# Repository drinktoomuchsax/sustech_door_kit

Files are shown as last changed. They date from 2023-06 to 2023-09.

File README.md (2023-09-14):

<div>
<p align="center">
<a href="https://www.pixilart.com/art/sustech-door-kit-logo-sr20129901307f3" >
  sustech_door_kit_logo
</a>
  </p>  
<h1 align="center">
  南科大宿舍门锁套件
</h1>
<p align="center">
  丢掉你的校园卡
</p>
<p align="center">
人脸识别、模糊密码、电子反锁、访客密码、无痕恢复……</a>
</p>
</div>

_This page is not available in [English](README.en.md) yet._ 

                                                   

:unlock:这个项目使用两片ESP32开发板以及一系列模块，将宿舍开门体验提到了新高度

:star:欢迎Star

:+1:项目采用CC0协议，欢迎复刻、商用、传播

:poop:假如你想在此基础上开发新功能，看不懂屎山代码或有任何疑惑，欢迎issue

---

# :world_map:Table of Contents
- [功能](#功能)
- [原理](#原理)
- [复刻](#复刻)
  - [:money\_with\_wings:物料清单（全功能-预算敏感版本）](#money_with_wings物料清单全功能-预算敏感版本)
  - [:wrench:所需工具](#wrench所需工具)
  - [门的部分](#门的部分)
  - [门内模块（inModule）](#门内模块inmodule)
  - [门外模块（exModule）](#门外模块exmodule)
- [To Do](#to-do)

# 功能
![face recognition gif]()
![keyboard gif]()
![password define]()
![lock cant open gif]()
![random password generator]()
![single eye lock gif]()

# 原理
拆开门发现有调试的线，详见[博客](wait-to-be-writed)

# 复刻
本项目在开始之初的设计目标之一就是尽可能低的复刻门槛，所以使用的都是现成的市售模块。虽然牺牲了一些集成度和成本，但是你不需要经历繁复地采购和焊接贴片元件，只需少许简单焊接和组装就能复刻本项目。

如果对某一步的详细程度感到不满意或有任何疑惑，欢迎提交issue。

如果你的网络有问题不能加载出图片，可以看南科手册上的版本。

## :money_with_wings:物料清单（全功能-预算敏感版本）
> 第一步，下面全部买回来

| n | 名称 | 数量 | 款式 | 总价 | 链接 | 备注 |
| --- | --- | ---- | --- | --- | --- | --- |
| 0 | luat esp32-s3开发板 | 1片  | ESP32S3开发板 | ￥29.9 | [淘宝合宙旗舰店](https://item.taobao.com/item.htm?spm=a1z09.2.0.0.67002e8dnQlfYj&id=696836421009&_u=53t2jj8gb611) | 可以换其他家，但是记得修改pcb封装尺寸和代码引脚定义 |
| 1 | luat esp32-c3开发板 | 1片  | 经典款ESP32C3开发板 | ￥12.9 | [淘宝合宙旗舰店](https://item.taobao.com/item.htm?spm=a1z09.2.0.0.67002e8dnQlfYj&id=666579064570&_u=53t2jj8g0ed4) | 同上 |
| 2 | 人脸识别模块HLK-FR1002 | 1个  | 【强力推荐】测试套件B: FR1002单模块+端子连接线*1 | ￥72.5 | [淘宝海凌科旗舰店](https://detail.tmall.com/item.htm?id=693925937468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) | |
| 3 | 雷达模块HLK-LD2420 | 1个  | 【LD2420单模块】24G雷达模块（人体移动微动感应）  | ￥9.9 | [淘宝海凌科旗舰店](https://detail.tmall.com/item.htm?id=703242126067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) | |
| 4 | 内模块pcb打板 | 1片  | 略 | ￥20 | [Gerber文件](pcbDesign/imModule/inModule_Gerber.zip) | 嘉立创价格，可以换其他家，洞洞板手焊（￥2.5），立创eda抄板白嫖（￥0） |
| 5 | 外模块pcb打板 | 1片  | 略 | ￥40左右 | [Gerber文件](pcbDesign/exMoudle/sustech_door_kit-exModule-Gerber.zip) | 同上，但是需要两片，一片用作焊接，一篇用作背板安装 |
| 6 | 继电器 | 1个  | 4路5v红板 | ￥12 | [淘宝优信电子](https://item.taobao.com/item.htm?spm=a1z09.2.0.0.67002e8dnQlfYj&id=549692985984&_u=53t2jj8gef8e) | 要买5v的，不然不能开发板直接触发 |
| 6.1 | 16pin排母 | 6个  | 1*16P单排母座 | ￥1 | [淘宝优信电子](https://item.taobao.com/item.htm?spm=a230r.1.14.22.43cb7ce2fQNwRq&id=522579376259&ns=1&abbucket=13#detail) | 用来插开发板的。测试供电正常再插上去，不然会烧:(。并且如果每次更新固件都要整个拆下来，麻烦发 |
| 7 | :keyboard:轴体 | 14个 | cherryMX的封装就能够焊上，具体轴体按需选择 | ￥10 | [淘宝不知名店铺](https://item.taobao.com/item.htm?spm=a1z09.2.0.0.67002e8dnQlfYj&id=626986550029&_u=53t2jj8g20a3) | |
| 8 | :keyboard:键帽 | 12个 | 标准的十字孔能插上轴体就行 | ￥6.3 | [桃堡~或者去网吧悄悄扣走windows键~](https://item.taobao.com/item.htm?spm=a21n57.1.0.0.33f6523cuvqG1C&id=704738471960&ns=1&abbucket=0#detail) | 有实力可以加钱上点好的 |
| 9 | :nut_and_bolt:M3x25螺丝 | 5个  | 直径3mm，长度25mm，0.5螺距 | ￥0.3 | [1688](https://detail.1688.com/offer/572533111204.html?spm=a2615.2177701.autotrace-smt_offerGeneral.6.20a22b78zPF4M8) | 其实3个就够了，剩下2个惩罚不仔细看备注的强迫症 |
| 10 | :nut_and_bolt:M3x？？螺丝 | 4个  | 长度？？mm，其余同上 | ￥5.2 | [1688](https://detail.1688.com/offer/572533111204.html?spm=a2615.2177701.autotrace-smt_offerGeneral.6.20a22b78zPF4M8) | 算上邮费 |
| 11 | :nut_and_bolt:M3螺母 | 4个  | 直径M3，六角对边长5.5mm，螺距0.5mm，2.4mm厚 | ￥0.2 | [1688](https://detail.1688.com/offer/572533111204.html?spm=a2615.2177701.autotrace-smt_offerGeneral.6.20a22b78zPF4M8) | 邮费算在上面了 |
| 12 | :nut_and_bolt:M3防松螺母  | 3个  | 长度？？mm，其余同上 | ￥0.2 | [1688](https://detail.1688.com/offer/572533111204.html?spm=a2615.2177701.autotrace-smt_offerGeneral.6.20a22b78zPF4M8) | 用来分隔继电器和内模块，邮费算在上面了 |
| 13 | :electric_plug:硅胶线 | 4条  | 统一1m，18AWG；红色、黑色、黄色、白色 | ￥6 | [桃堡](https://item.taobao.com/item.htm?spm=a1z09.2.0.0.67002e8dnQlfYj&id=654286714565&_u=53t2jj8g48c8) | |
| 14 | :electric_plug:CtoC数据线 | 1条  | 1m左右就好 | ￥6 | [桃堡](https://detail.tmall.com/item.htm?id=662435210626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) | 如果你经常有连接开发板的需求，推荐合宙的[10条各种版本打包](https://item.taobao.com/item.htm?spm=a1z10.5-c-s.w4002-24045920841.24.230e5aa3n5OKyx&id=706207670841) |
| 15 | DC-DC模块 | 1个  | 链接里就一个，买他就好 | ￥5.7 | [桃堡](https://item.taobao.com/item.htm?spm=a1z09.2.0.0.35b32e8dcWQ58H&id=536347025767&_u=53t2jj8g6082) | |
| **666** | **总计** | | | **￥240左右** |

### :moneybag:物料清单（删减功能-预算敏感版本）
如果上述BOM超过了你的预算，可以通过删减功能来减少部件，比如可以删减掉人脸识别功能，避免购买HLK-FR1002和HLK-LD2420将价格减到**153元**。

或者可以eda抄板，节省打板价格。**注意，外模块尺寸为5*13cm，不在立创优惠劵的尺寸范围内，可以试着删减掉人脸识别后将尺寸缩小。**

砍掉一些功能，花上几个小时抄板，修改一下代码，理论最低预算为**86元**。

## :wrench:所需工具
> 如果只是为了复刻项目，下面这些工具不用全部买回来，想办法借到比较合理。但这是个社恐友好的项目，所以放上一些参考购买链接。

| 名称 | 用途 | 参考购买链接 |
| --- | --- | --- |
| 剥线钳 | 剥线 | [【简装】7寸单色手柄剥线钳](https://detail.tmall.com/item.htm?abbucket=0&id=43540267171&ns=1&spm=a21n57.1.0.0.1f6d523cvhBHgo) |
| 烙铁 | 焊接 | [标配+C2C数据线+转接板+氮化镓充电器+K65小刀头+BC2尖头 ](https://detail.tmall.com/item.htm?id=662514528915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) |
| 焊锡 | 焊接 | [含锡40%线径0.8mm-50克](https://detail.tmall.com/item.htm?id=595763429832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) |
| 十字螺丝刀 | 打螺丝 | [5*75十字【专业款】](https://item.taobao.com/item.htm?spm=a21n57.1.0.0.33f6523cuvqG1C&id=709830788462&ns=1&abbucket=0#detail) |
| 扳手 | 打螺母 | [【中小型】活扳手/管钳双功能两用8寸-200mm](https://detail.tmall.com/item.htm?id=655191633412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) |
| 胶布 | 防止短接 | 是个胶布就行 |
| 美工刀或笔刀 | 剥线 | 最好锋利一点 |
| 热熔胶枪 | 加固剥线处 | [50W豪华小胶枪+ 10胶棒](https://detail.tmall.com/item.htm?id=559404680156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) |

## 门的部分
### 1.拆门

> 首先，这部分不适合一个人，建议你找一个室友帮忙

> **门只能从内部拆开，平时能够看到2颗裸露的螺丝，大胆地拆。**

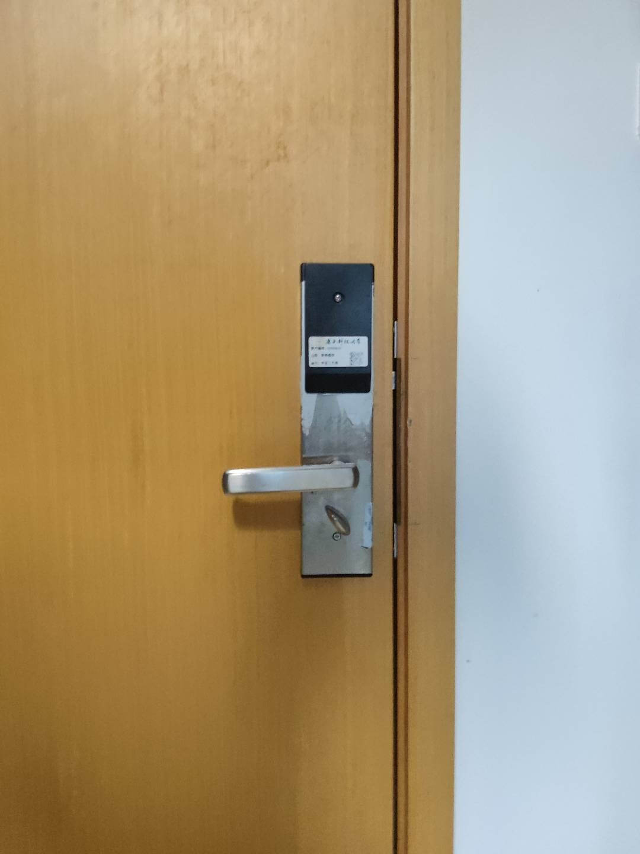
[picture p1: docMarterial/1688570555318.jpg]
一上一下正好两个


> **拆开后把塑料外壳取下，能看到三颗螺丝,前面两颗，后面一颗。拆掉前面两颗整个把手就会掉下来。**

> 这时你应该可以看到内门把手小锁的销被取走了，这就是我们不能从里面反锁的原因。网上没找到合适的，你有时间可以自己建模3D打印一个就能重新获得机械反锁门的能力。

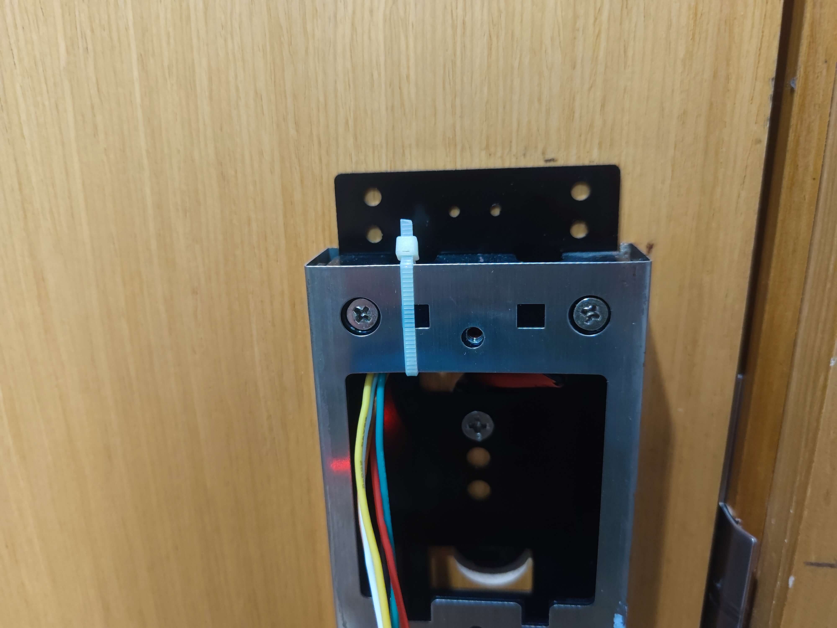
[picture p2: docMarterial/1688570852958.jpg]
前面两颗，后面一颗


> 因为这部分是后写的，有一些照片因为安装了内模块不能继续拍，sorry

> **内门把手掉下来后，会露出一个框架，有两颗螺丝，这两颗螺丝固定内框架和外门把手**

> 下图是一个，还有一个在更下方

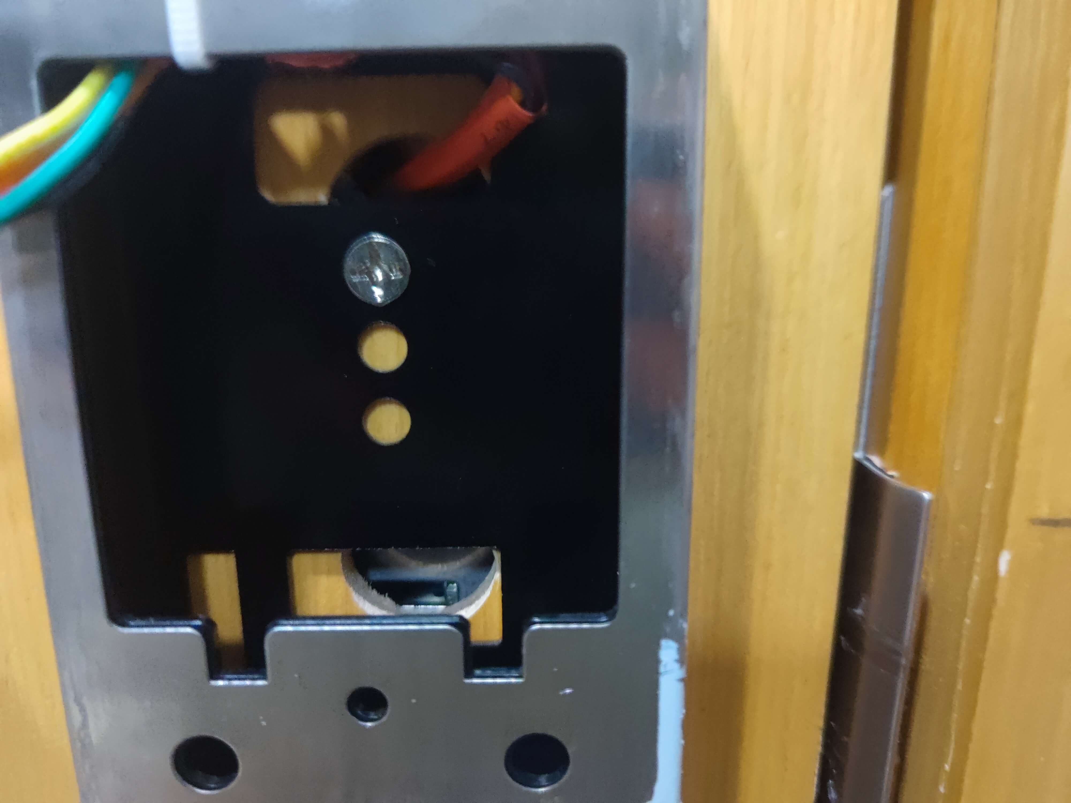
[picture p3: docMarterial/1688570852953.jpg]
上方的螺丝


> **一手扶着外门把手，一手拆内框架的螺丝**

> **螺丝拆下来后，内框架会掉下来，外门把手也会掉下来**

> **你应该可以看到掉下来的外门把手框里有一些线连到门里面（忽略图片左方的凝固的热熔胶）**

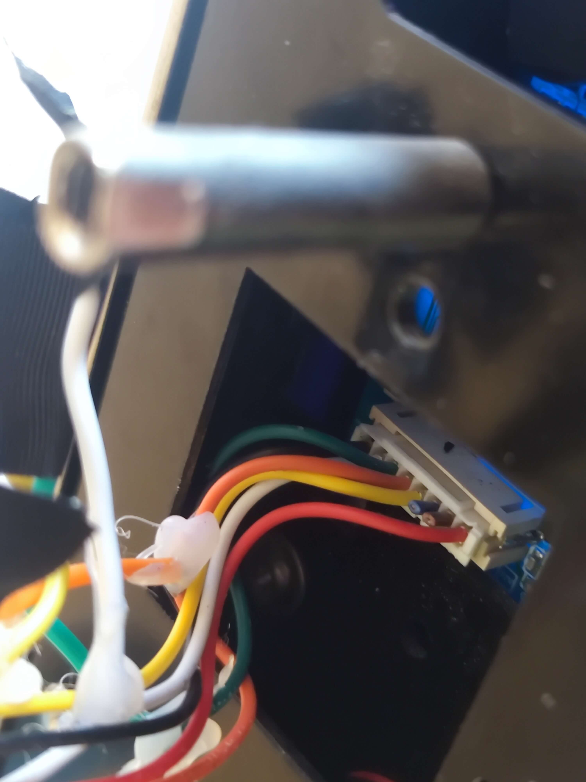
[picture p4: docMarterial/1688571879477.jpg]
线们


> **这些线有不同的功能，红线12v供电、黑线地，其他四个颜色短接地会有不同的效果，效果如下表**

| 短接 | 效果 |
| ---- | --- |
| 黑橙 | 面板变绿，正常开门 |
| 黑绿 | 锁门（面板保持蓝色） |
| 黑黄 | 开门 |
| 黑白 | 锁门（面板变红） |

> **你已经看到线了，进入下一步，剥线！**

### 2.剥线

> **这是一个手艺活，比较考验耐心**

> **你需要用美工刀或者笔刀将线的外层剥开，露出里面的金属。注意不要直接切断，特别是红色和黑色的电源线，没人知道这个系统断电重启之后还可能会出现哪些问题**

> **项目只会用到4根线，分别是红色、黑色、黄色、白色。所以你只需要剥4根线**

### 3.焊接延长线

> 这一步可能会比较难

> **线剥好后，剪下你买的[硅胶线](https://item.taobao.com/item.htm?spm=a1z09.2.0.0.67002e8dnQlfYj&id=654286714565&_u=53t2jj8g48c8)，长度需要自己估计一下，大概40cm（估计值，绝对不准）。用[剪线钳](https://detail.tmall.com/item.htm?abbucket=0&id=43540267171&ns=1&spm=a21n57.1.0.0.1f6d523cvhBHgo)剥去两头的线。一端镀锡，一端缠胶布备用**

> **然后给外门把手剥线的地方也镀上锡**

> **然后把对应颜色的线焊上**

> **打上热熔胶防止短接同时加强连接处**

> **最后效果如下（方便研究我把所有都剥了）**

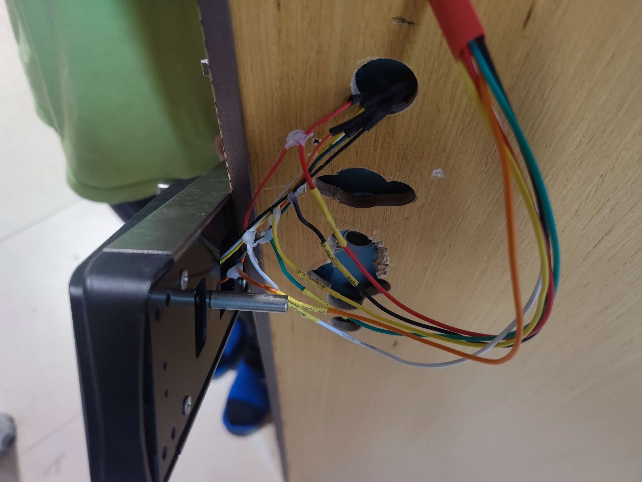
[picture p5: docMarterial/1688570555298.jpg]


### 4.走线
> **把线首先穿过外门把手上面的小框**

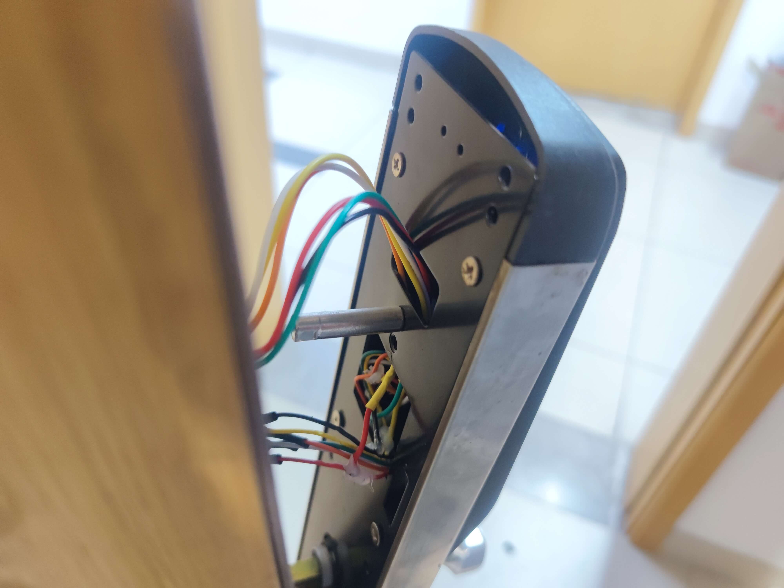
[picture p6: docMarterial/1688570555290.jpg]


> **然后穿过门上的洞，这样外门把手就不会因为线的存在而不能贴合门体**

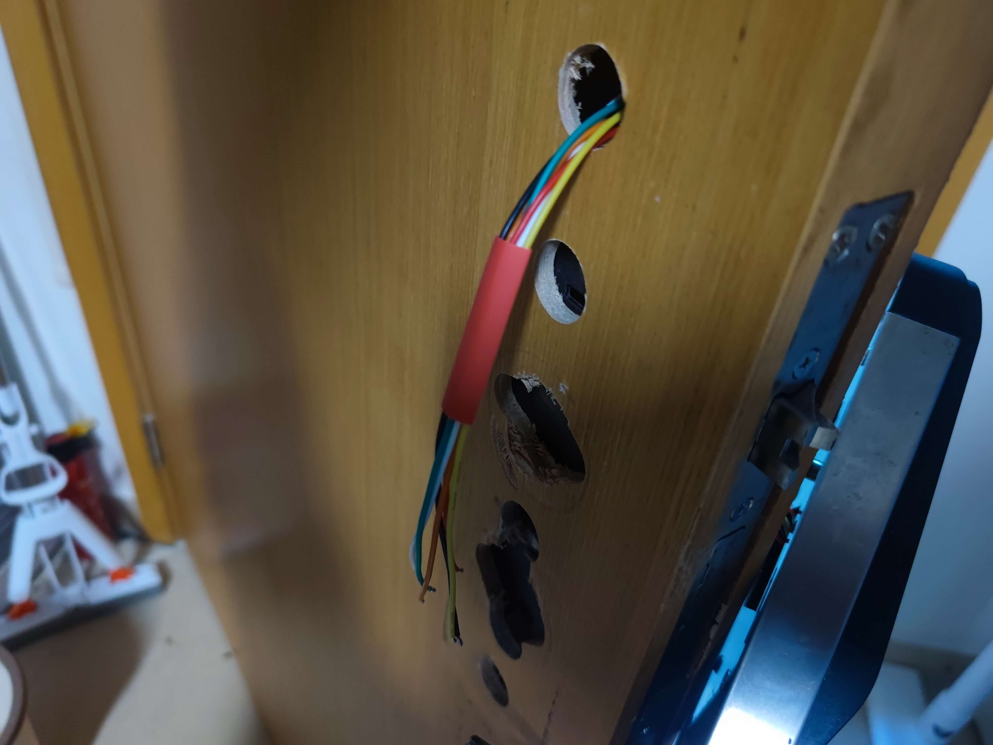
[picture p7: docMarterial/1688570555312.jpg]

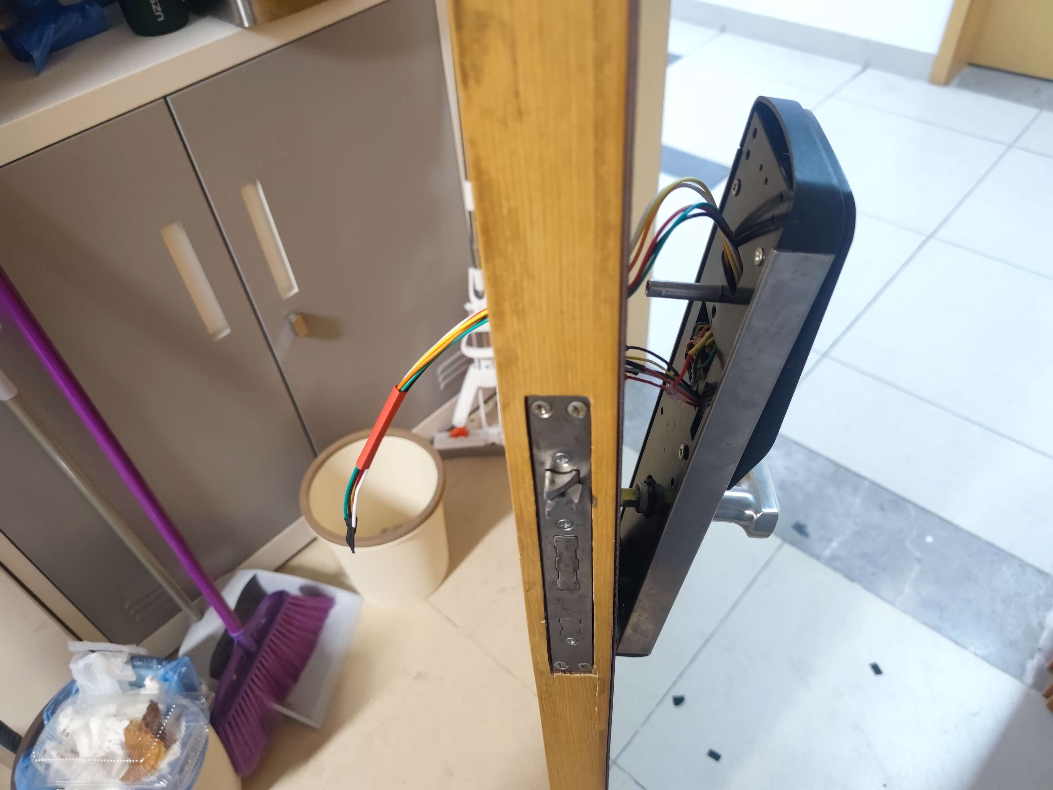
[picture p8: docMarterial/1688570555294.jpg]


> **最后效果如下，平整度没有差别**

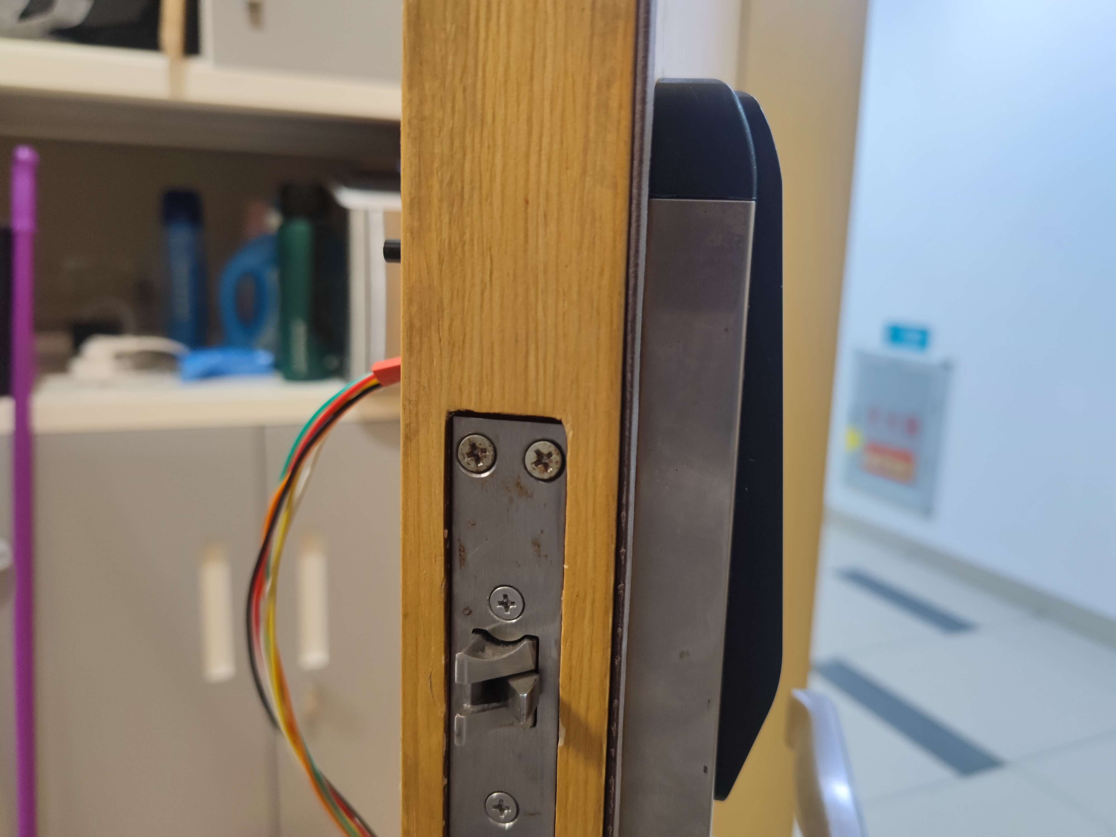
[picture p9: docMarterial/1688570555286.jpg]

### 5.装门

> **然后就是逆向装回去的过程，不多说了**

> **唯一值得注意的点是，可以用一段胶布缠上整束线，然后用一个扎带固定，这样就把拉力转移到扎带部分而不是焊点** 

zipper

> **最后效果如下**

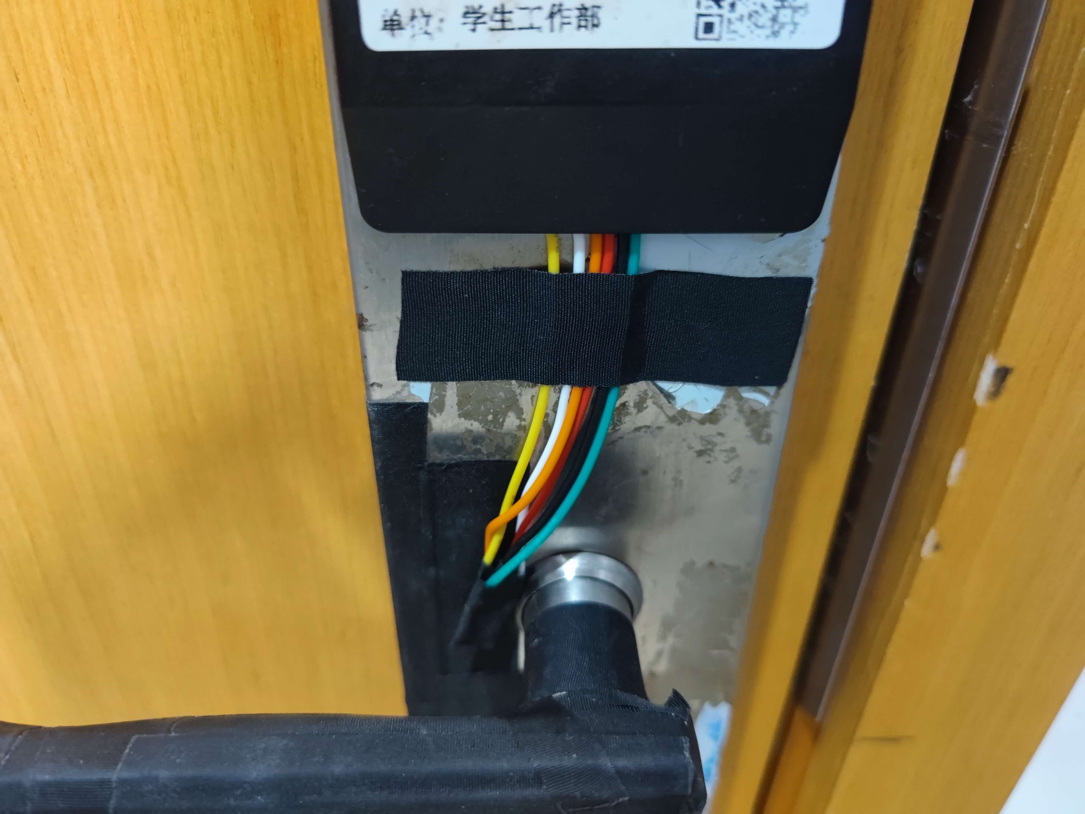
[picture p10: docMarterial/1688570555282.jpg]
cables on the door


> 至此拆门部分结束

## 门内模块（inModule）

### 1.焊接
#### a.开发板排母
#### b.排线
### 2.开发板刷入程序
#### a.更改参数
- bleServerName
- BLE UUIDs
- WiFi name
- WiFi pswd
- realpswd
- 
### 3.安装
#### a.继电器接门内地线
#### b.继电器接开发版控制线、电源线、地线
#### c.测试输出电压
#### d.安装开发板
#### e.热熔胶胶固定
#### f.焊接门内12v电源线

### 4.测试
#### a.WiFi开门功能
#### b.按键功能

## 门外模块（exModule）
### 1.焊接
#### a.电阻、开发板
#### b.雷达、排针
#### c.人脸识别模块

### 2.组装
### 3.开发板刷入程序
#### a.更改参数
### 4.配置模块
#### a.人脸注册
#### b.修改雷达门限
### 5.调试

# To Do
对功能有任何想法和提议，都欢迎提交issue。当然，保证不保证解决。
- [ ] 完善文档
- [ ] 接入homeassistant，让小爱同学开门
- [ ] 通信协议
- [ ] 剩下的两根线
- [ ] 更多的功能
- [ ] 更低的复刻门槛

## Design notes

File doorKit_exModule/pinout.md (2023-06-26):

|IO选择|对应功能|IO编号|启动项相关|ADC|DAC|UART|Touch|SPI/IIC|
|:----|:----|:----|:----|:----|:----|:----|:----|:----|
| | |GPIO0|下载：低电平/启动：高电平|ADC2_1| | |TP_1| |
| | |GPIO1| | | |TX0| | |
| | |GPIO2| |ADC2_2| | |TP_2| |
| | |GPIO3| | | |RX0| | |
|x|keyboardInput|GPIO4| |ADC2_0| | |TP_0| |
| | |GPIO5|启动时必须高电平| | | | |VSPI|
| | |GPIO6|连接了FLASH(CLK)| | | | | |
| | |GPIO7|连接了FLASH(SD0)| | | | | |
| | |GPIO8|连接了FLASH(SD1)| | | | | |
| | |GPIO9|连接了FLASH(SD2)| | |RX1| | |
| | |GPIO10|连接了FLASH(SD3)| | |TX1| | |
| | |GPIO11|连接了FLASH(CMD)| | | | | |
| | |GPIO12|启动时必须低电平|ADC2_5| | |TP_5|HSPI|
| | |GPIO13| |ADC2_4| | |TP_4|HSPI|
| | |GPIO14|启动时必须高电平|ADC2_6| | |TP_6|HSPI|
| | |GPIO15|启动时必须高电平|ADC2_3| | |TP_3|HSPI|
| | |GPIO16| | | |RX2| | |
| | |GPIO17| | | |TX2| | |
| | |GPIO18| | | | | |VSPI|
| | |GPIO19| | | | | |VSPI|
|x|keyboardOutput|GPIO21| | | | | |IIC_SDA|
|x|keyboardOutput|GPIO22| | | | | |IIC_SCL|
|x|keyboardOutput|GPIO23| | | | | |VSPI|
| | |GPIO25| |ADC2_8|DAC_1| | | |
| | |GPIO26| |ADC2_9|DAC_2| | | |
| | |GPIO27| |ADC2_7| | |TP_7| |
|x|keyboardInput|GPIO32| |ADC1_4| | |TP_9| |
|x|keyboardInput|GPIO33| |ADC1_5| | |TP_8| |
| ||GPIO34|Input Only|ADC1_6| | | | |
|x|keyboardInput|GPIO35|Input Only|ADC1_7| | | | |
| | |GPIO36|Input Only/SVP|ADC1_0| | | | |
| | |GPIO39|Input Only/SVN|ADC1_3| | | | |
| | |GND||| | | | |
| | |GND||| | | | |
| | |3V3||| | | | |
| | |VIN||| | | | |

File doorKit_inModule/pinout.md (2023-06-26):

|IO选择|对应功能|IO编号|启动项相关|ADC|DAC|UART|Touch|SPI/IIC|
|:----|:----|:----|:----|:----|:----|:----|:----|:----|
| | |GPIO0|下载：低电平/启动：高电平|ADC2_1| | |TP_1| |
| | |GPIO1| | | |TX0| | |
| | |GPIO2| |ADC2_2| | |TP_2| |
| | |GPIO3| | | |RX0| | |
|x|Touch pad|GPIO4| |ADC2_0| | |TP_0| |
| | |GPIO5|启动时必须高电平| | | | |VSPI|
| | |GPIO6|连接了FLASH(CLK)| | | | | |
| | |GPIO7|连接了FLASH(SD0)| | | | | |
| | |GPIO8|连接了FLASH(SD1)| | | | | |
| | |GPIO9|连接了FLASH(SD2)| | |RX1| | |
| | |GPIO10|连接了FLASH(SD3)| | |TX1| | |
| | |GPIO11|连接了FLASH(CMD)| | | | | |
| | |GPIO12|启动时必须低电平|ADC2_5| | |TP_5|HSPI|
| | |GPIO13| |ADC2_4| | |TP_4|HSPI|
| | |GPIO14|启动时必须高电平|ADC2_6| | |TP_6|HSPI|
| | |GPIO15|启动时必须高电平|ADC2_3| | |TP_3|HSPI|
| | |GPIO16| | | |RX2| | |
| | |GPIO17| | | |TX2| | |
| | |GPIO18| | | | | |VSPI|
|x|relay ouput|GPIO19| | | | | |VSPI|
|x|relay ouput|GPIO21| | | | | |IIC_SDA|
|x|relay ouput|GPIO22| | | | | |IIC_SCL|
|x|relay ouput|GPIO23| | | | | |VSPI|
| | |GPIO25| |ADC2_8|DAC_1| | | |
| | |GPIO26| |ADC2_9|DAC_2| | | |
| | |GPIO27| |ADC2_7| | |TP_7| |
| | |GPIO32| |ADC1_4| | |TP_9| |
| | |GPIO33| |ADC1_5| | |TP_8| |
| | |GPIO34|Input Only|ADC1_6| | | | |
| | |GPIO35|Input Only|ADC1_7| | | | |
| | |GPIO36|Input Only/SVP|ADC1_0| | | | |
| | |GPIO39|Input Only/SVN|ADC1_3| | | | |
|x|GND for relay|GND||| | | | |
|x|Powe in|GND||| | | | |
| | |3V3||| | | | |
|x|Power in|VIN||| | | | |

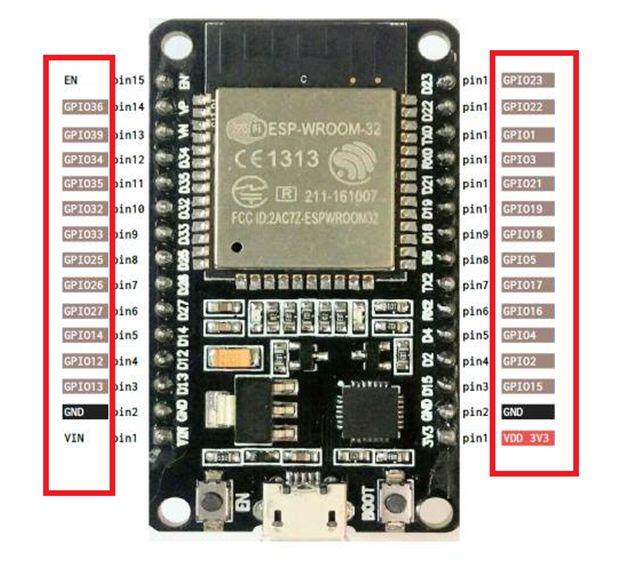
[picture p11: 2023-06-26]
tool/devKit/32S.jpg

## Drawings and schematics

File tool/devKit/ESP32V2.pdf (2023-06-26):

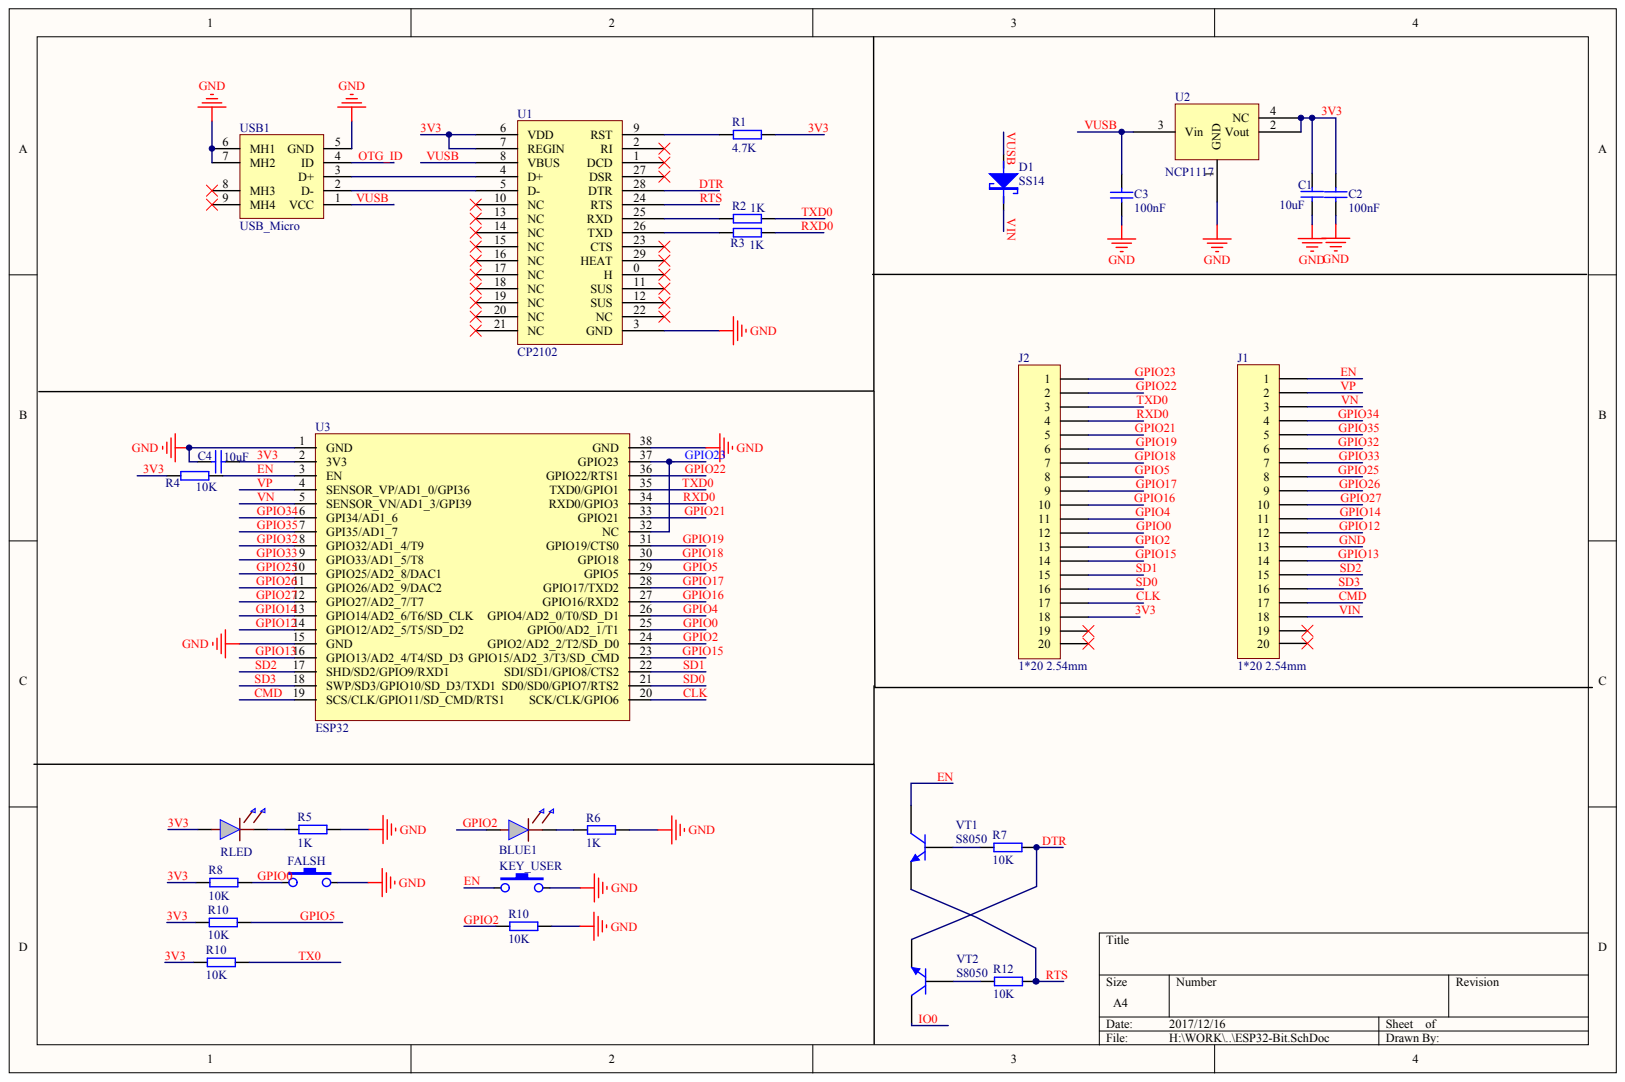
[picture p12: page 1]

GND 1 Vout 2 Vin 3 NC 4

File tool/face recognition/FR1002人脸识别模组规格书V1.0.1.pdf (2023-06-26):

# HLK-

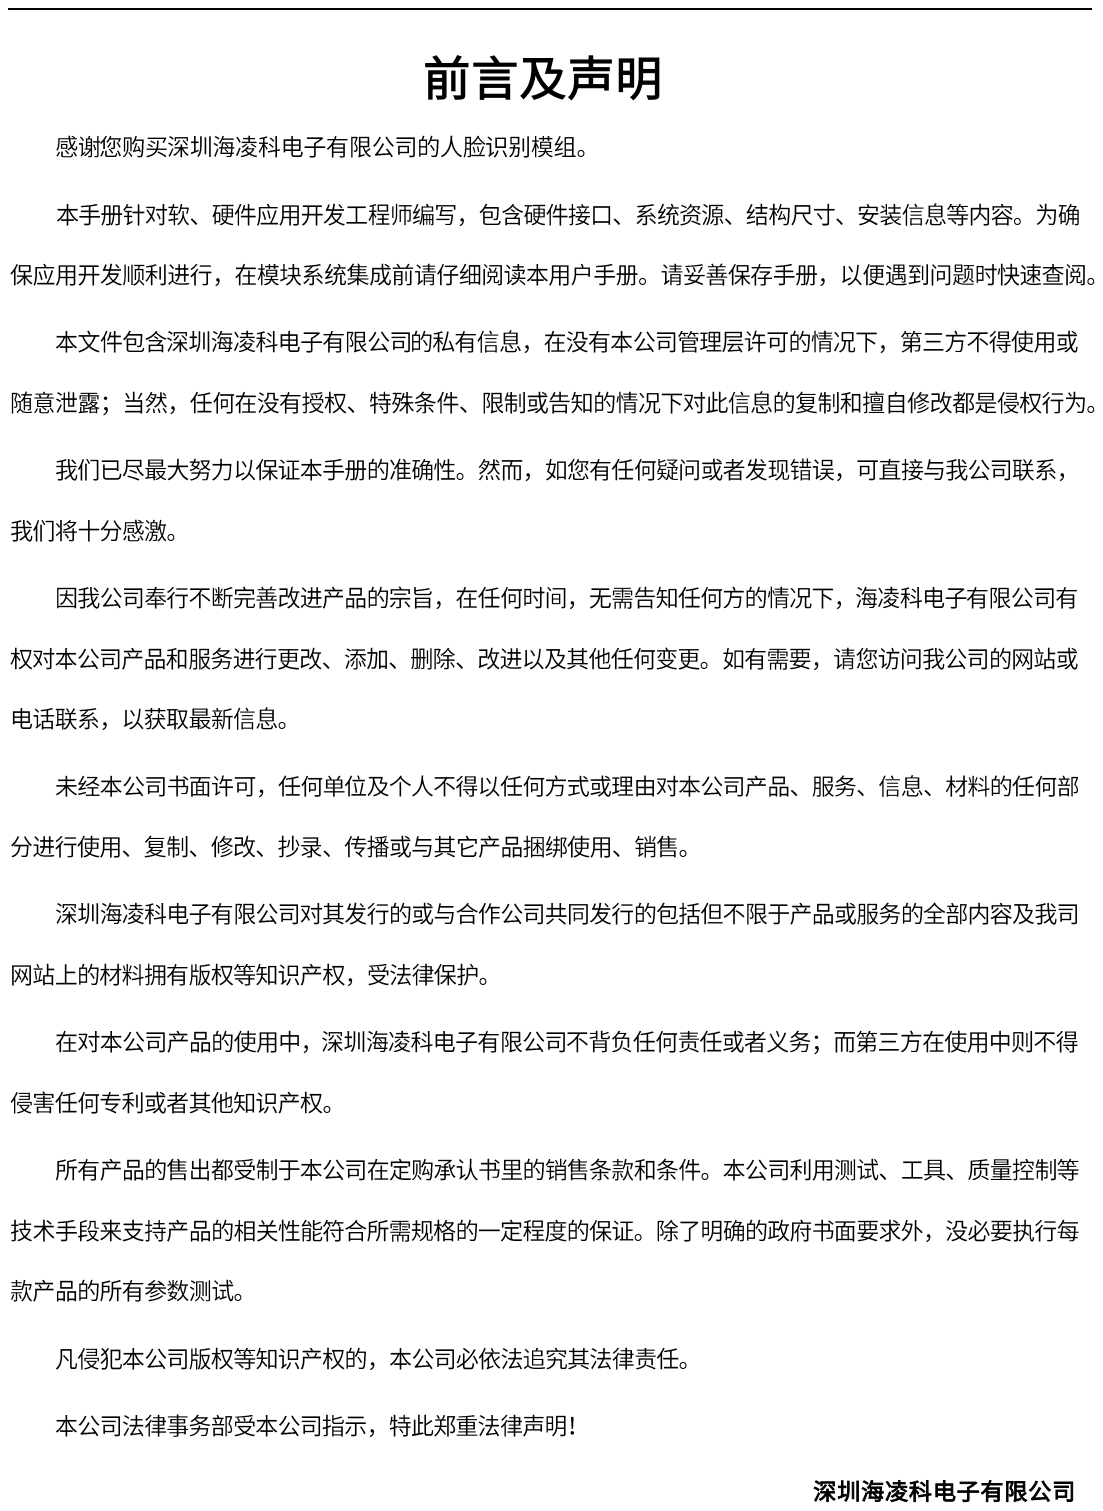
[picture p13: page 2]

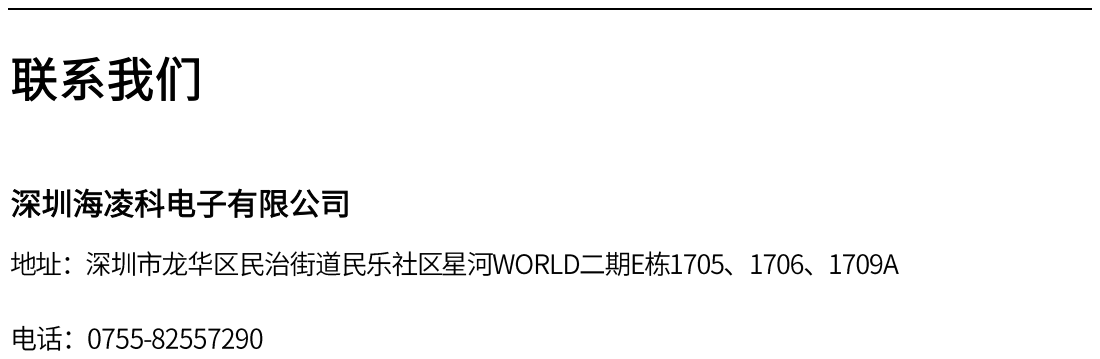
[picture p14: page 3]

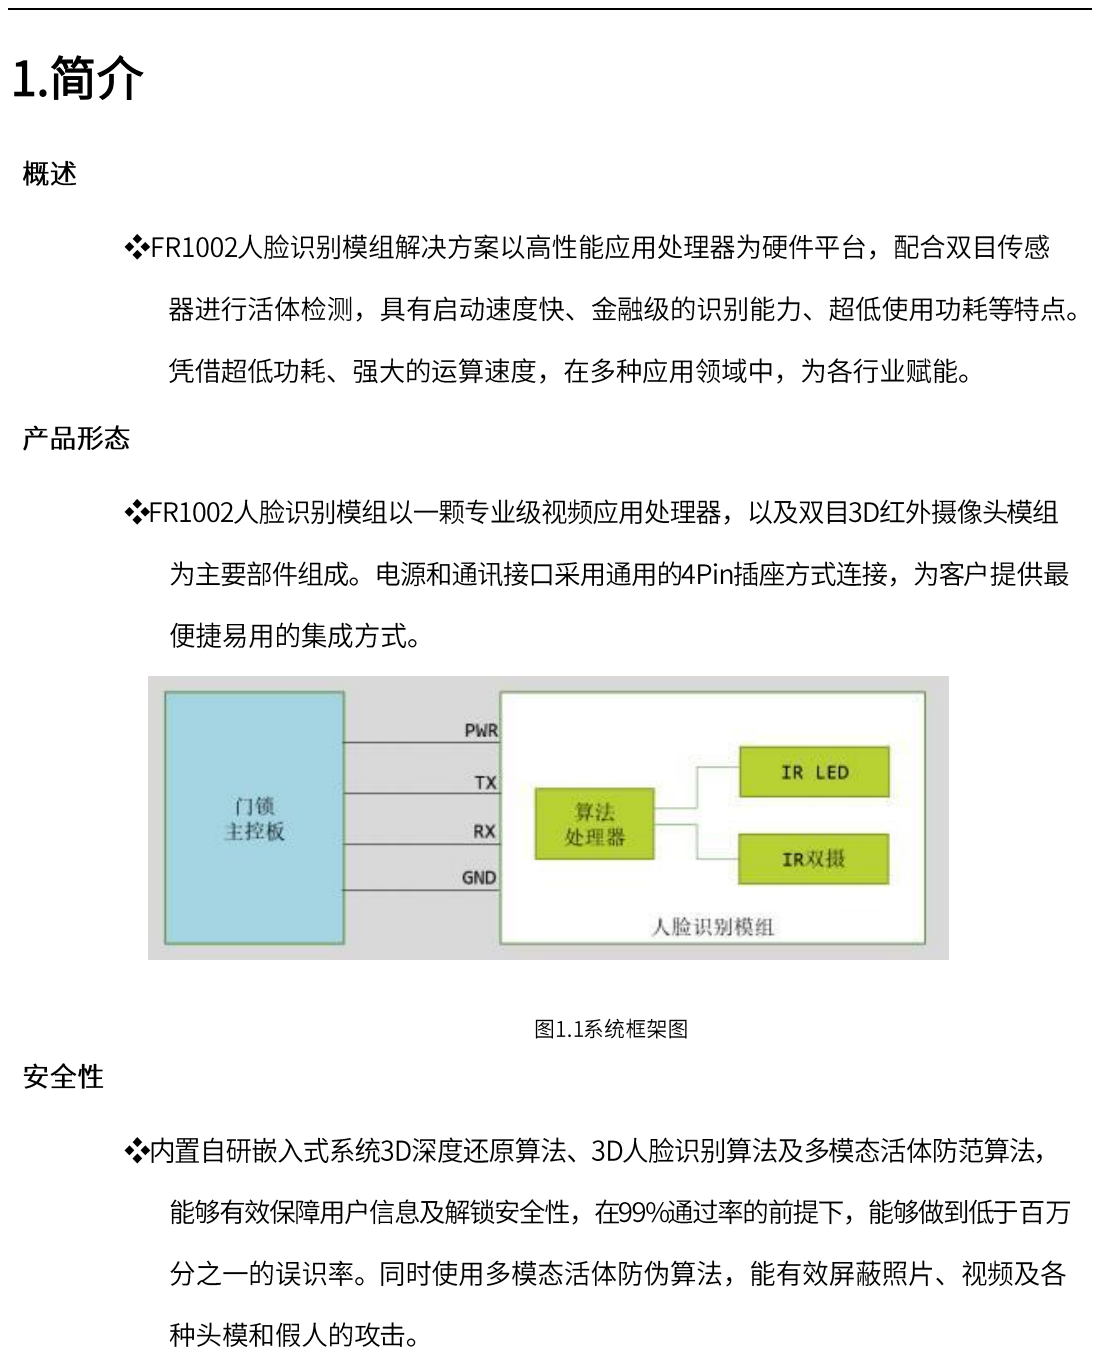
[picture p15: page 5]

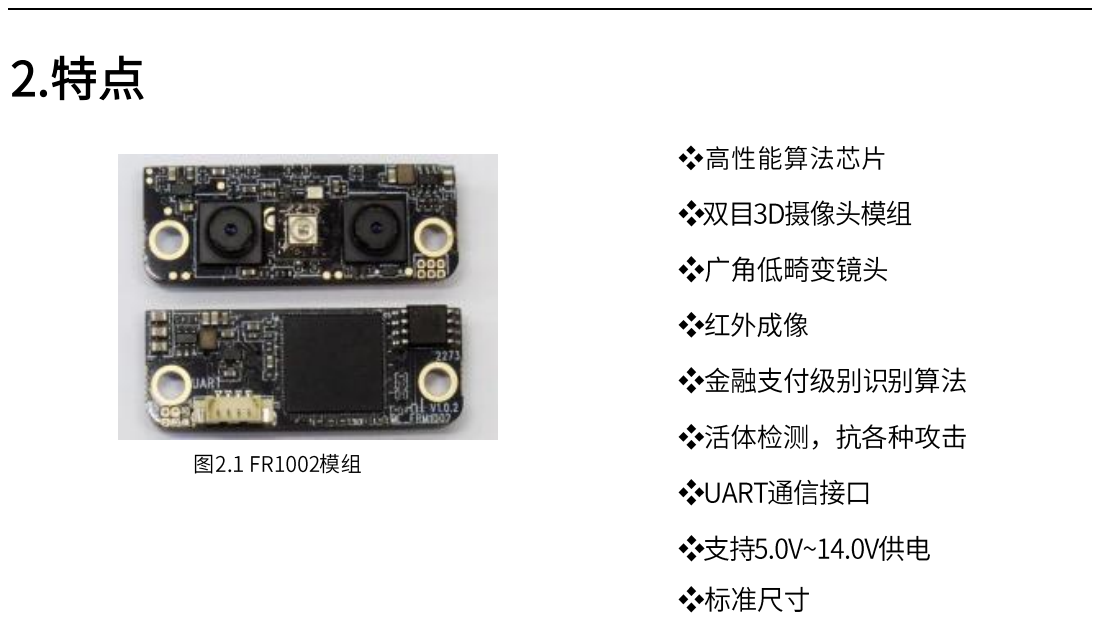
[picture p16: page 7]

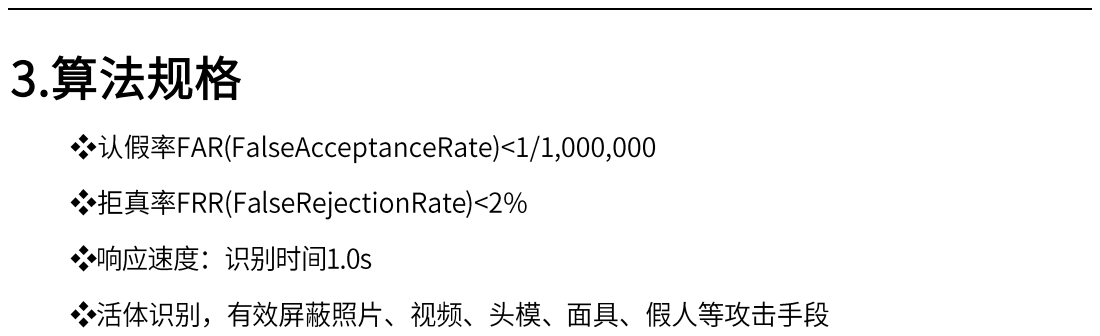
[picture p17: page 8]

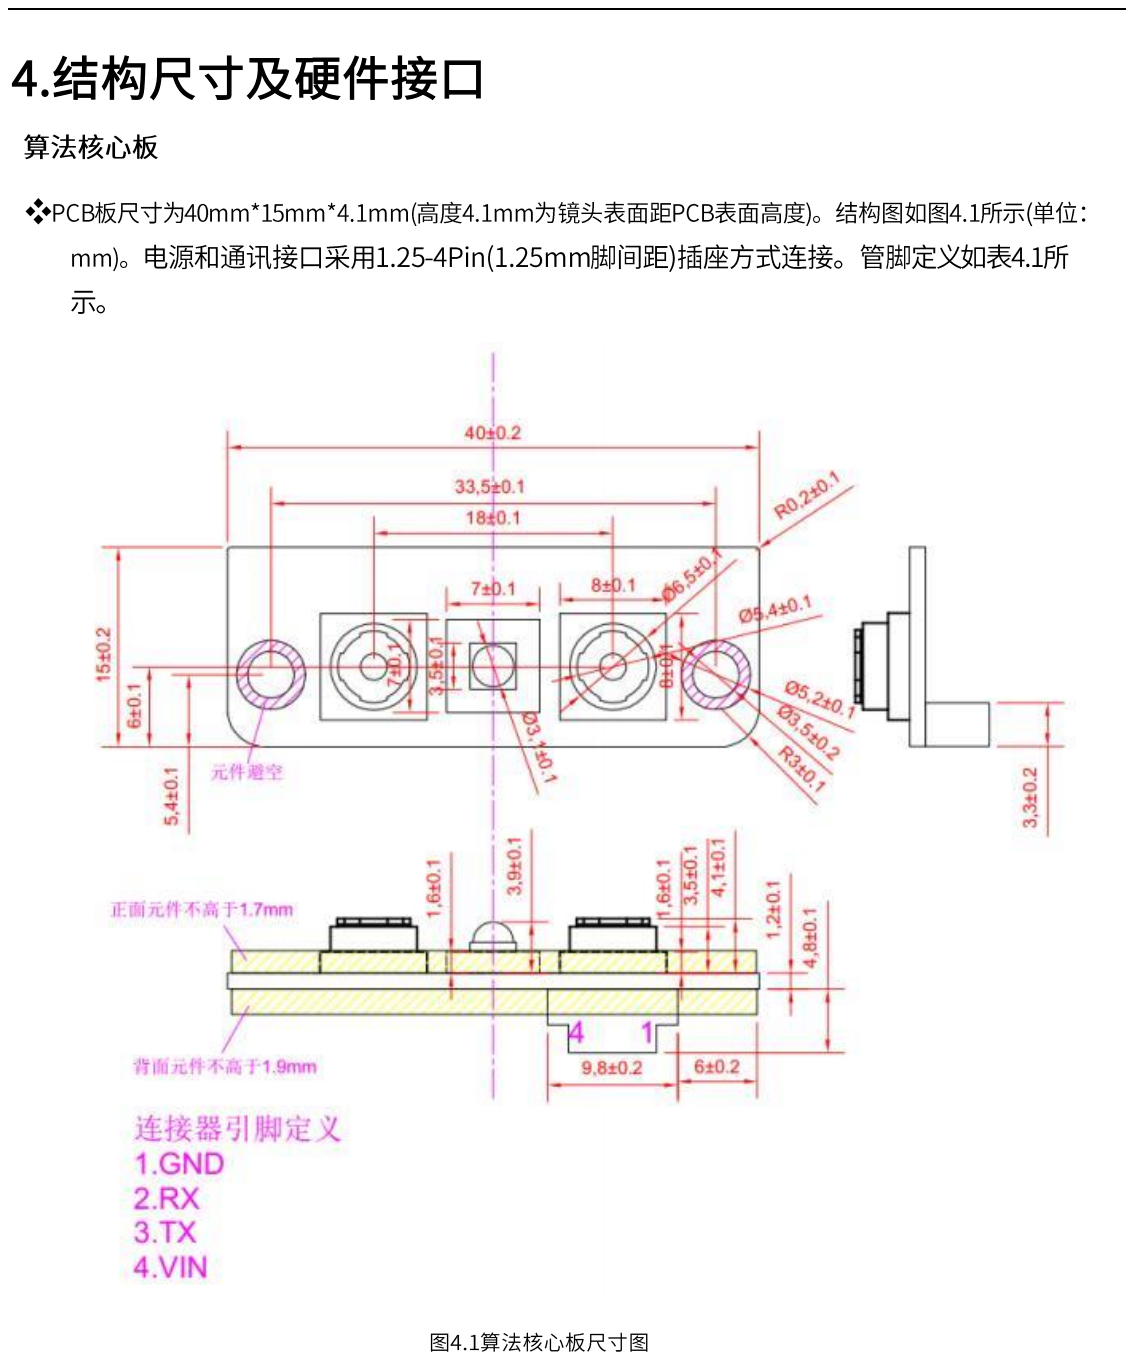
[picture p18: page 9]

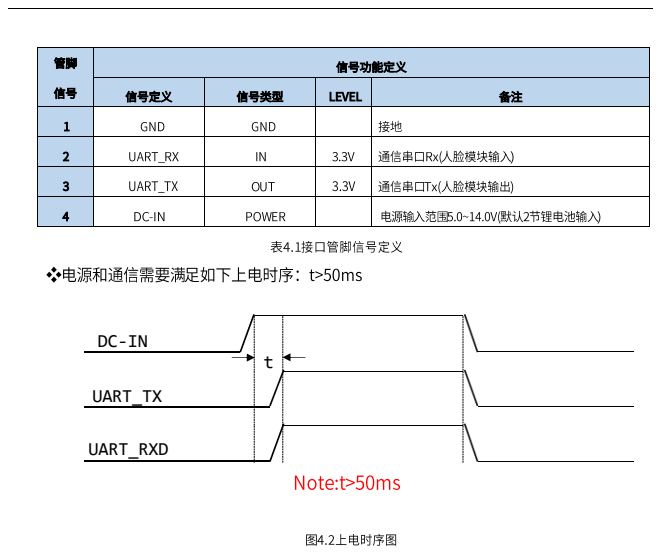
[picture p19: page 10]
UART_TX; UART_RXD

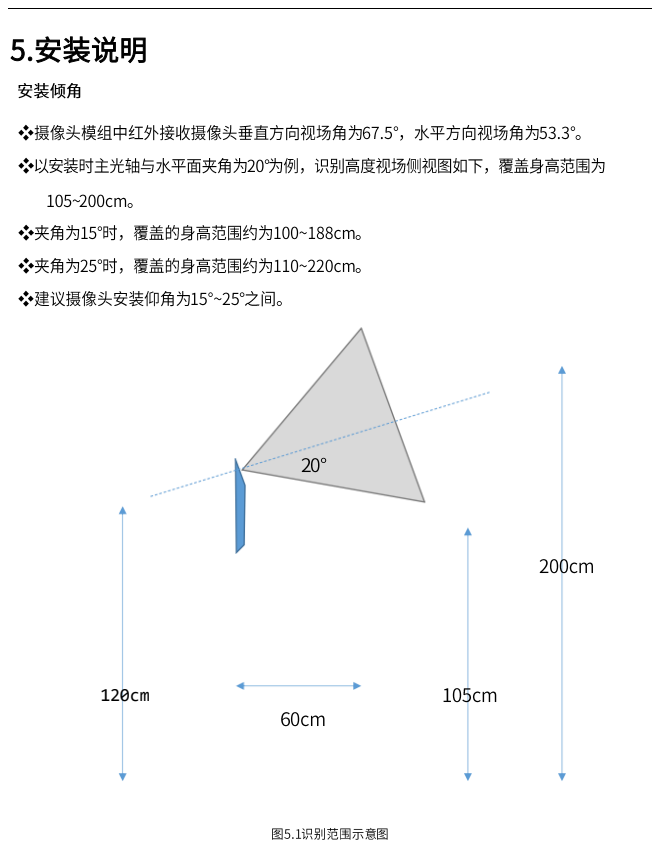
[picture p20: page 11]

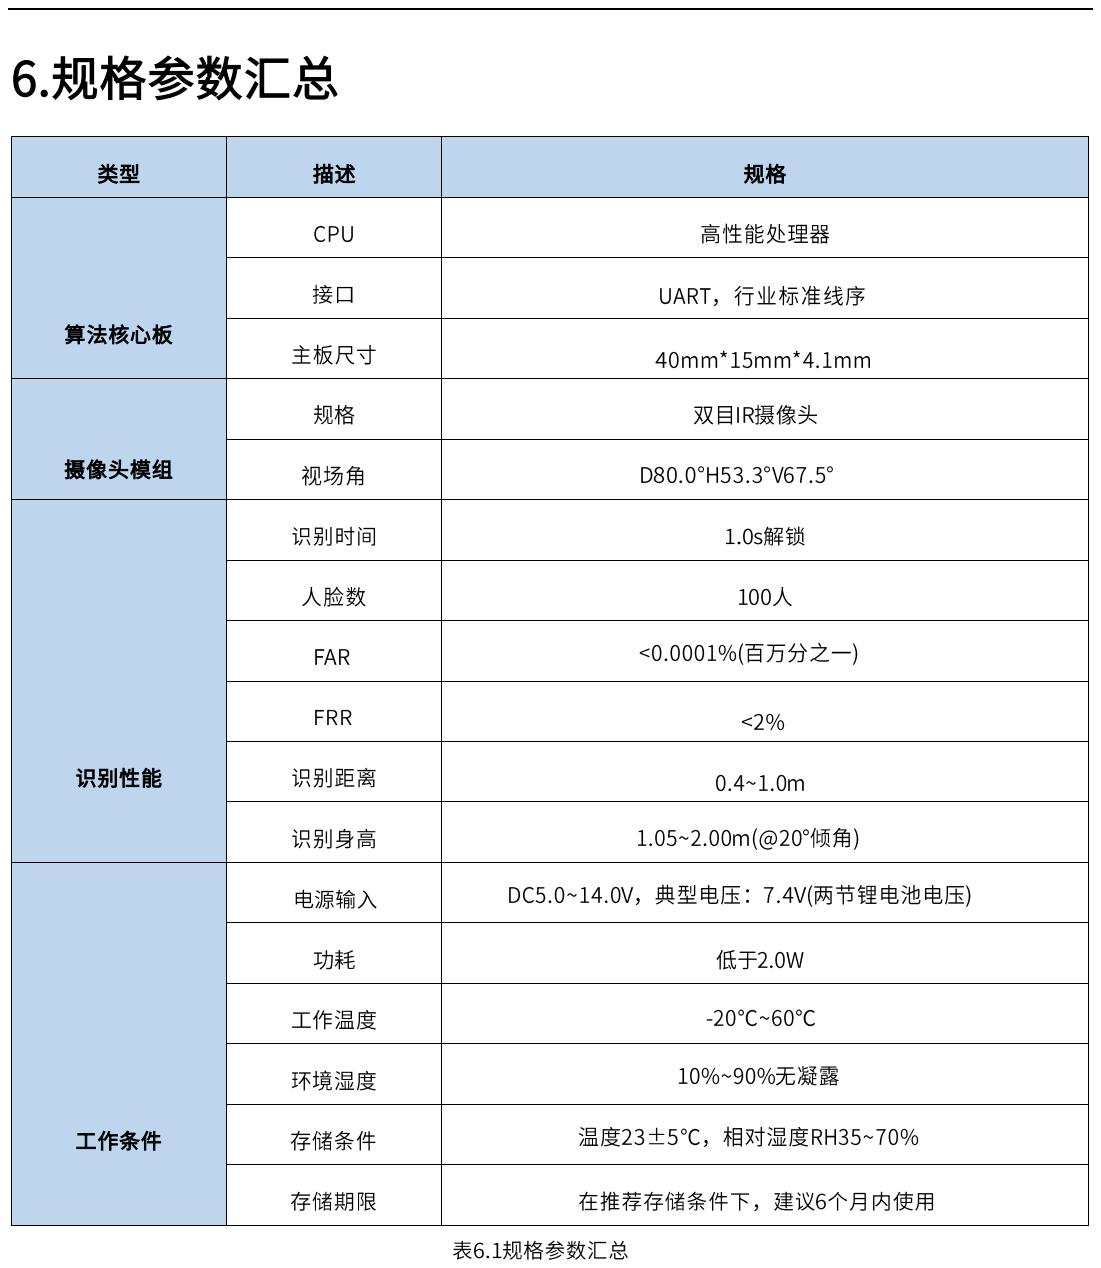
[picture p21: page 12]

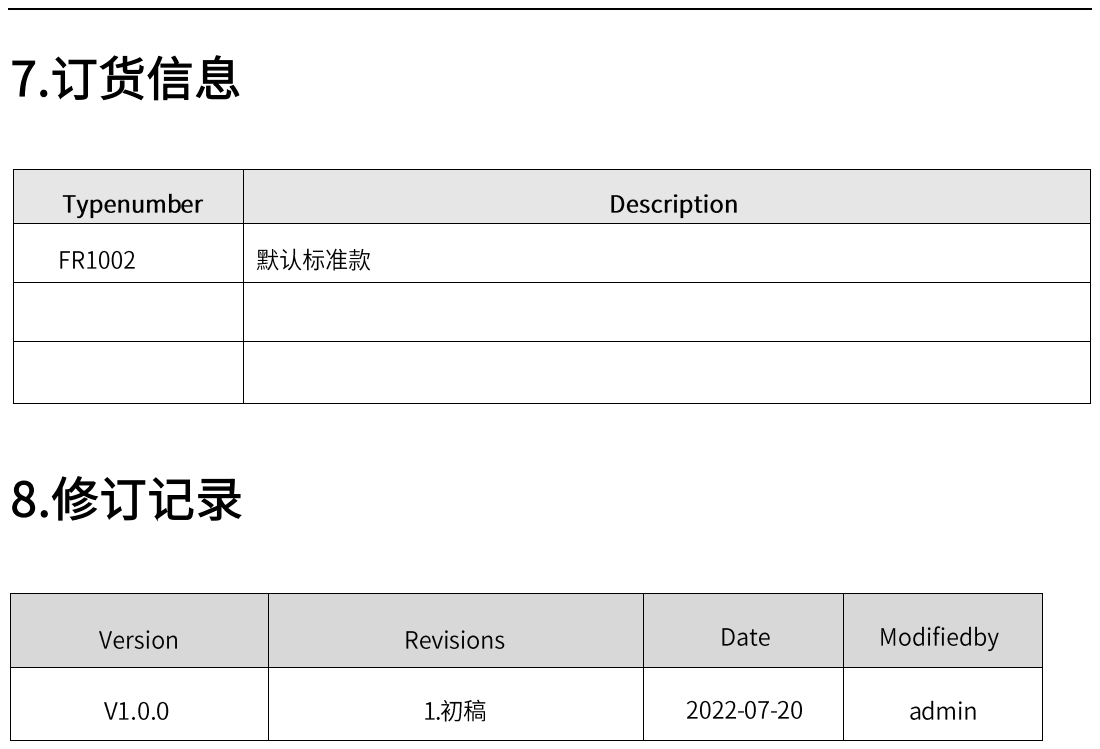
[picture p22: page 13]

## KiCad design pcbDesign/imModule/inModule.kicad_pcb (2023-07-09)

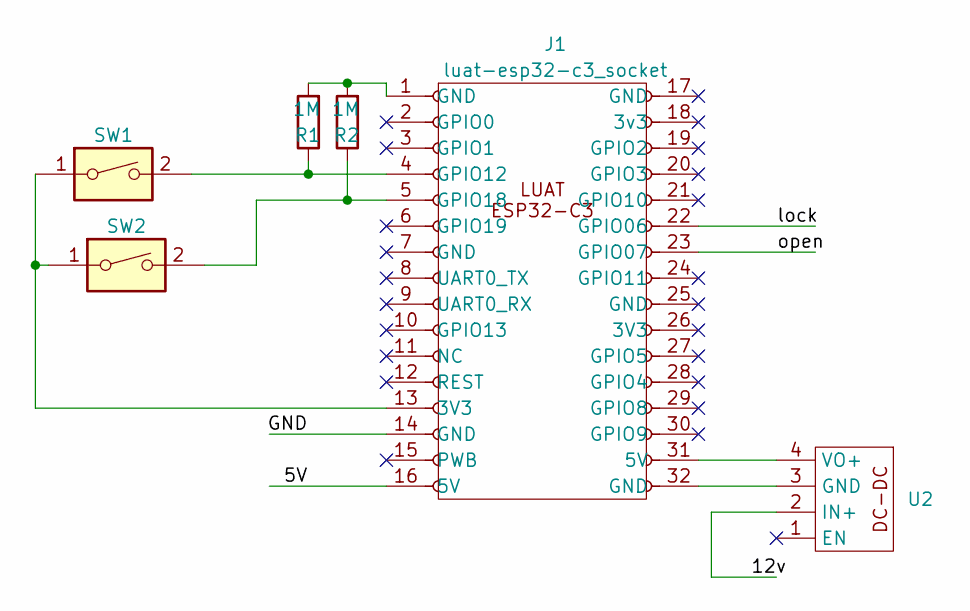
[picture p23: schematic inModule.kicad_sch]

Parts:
J1: luat-esp32-c3_socket; luat-esp32-c3-devBoard
R1, R2: 1M; R_Axial_DIN0207_L6.3mm_D2.5mm_P7.62mm_Horizontal
SW1, SW2: SW_DIP_x01; SW_Cherry_MX_1.00u_Plate
U2: taobaoDCDC

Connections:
/5V: J1.16 (5V)
/12v: U2.2 (IN+)
/GND: J1.14 (GND)
/lock: J1.22 (GPIO06)
/open: J1.23 (GPIO07)
unnamed: J1.13 (3V3), SW1.1, SW2.1
unnamed: J1.1 (GND), R1.2, R2.2
unnamed: J1.4 (GPIO12), R1.1, SW1.2
unnamed: J1.5 (GPIO18), R2.1, SW2.2
unnamed: J1.32 (GND), U2.3 (GND)
unnamed: J1.31 (5V), U2.4 (VO+)

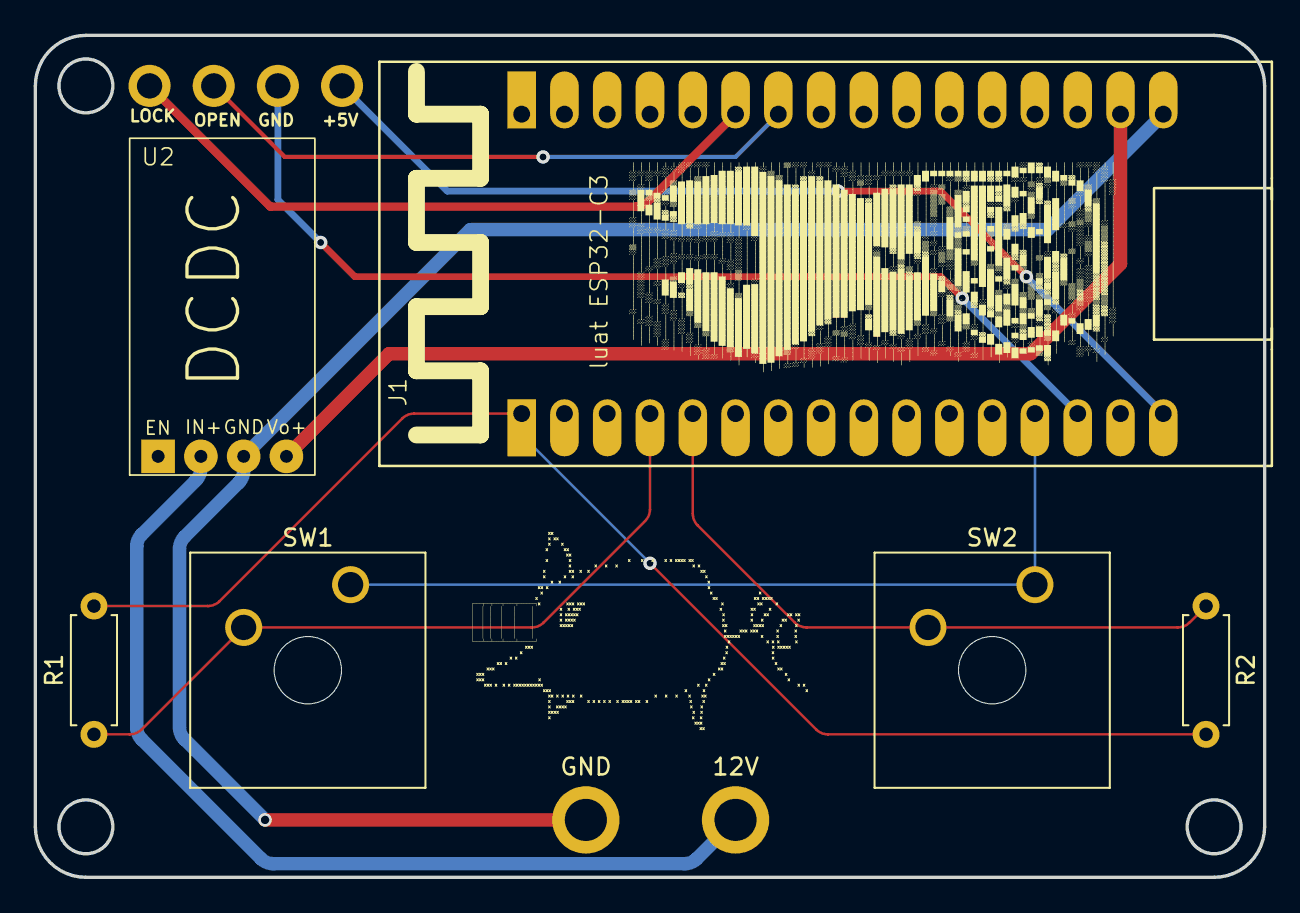
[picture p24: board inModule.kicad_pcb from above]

Board: 2 copper layers, 73.0 x 50.0 mm, 6 parts (0 on the bottom side), 6 nets.

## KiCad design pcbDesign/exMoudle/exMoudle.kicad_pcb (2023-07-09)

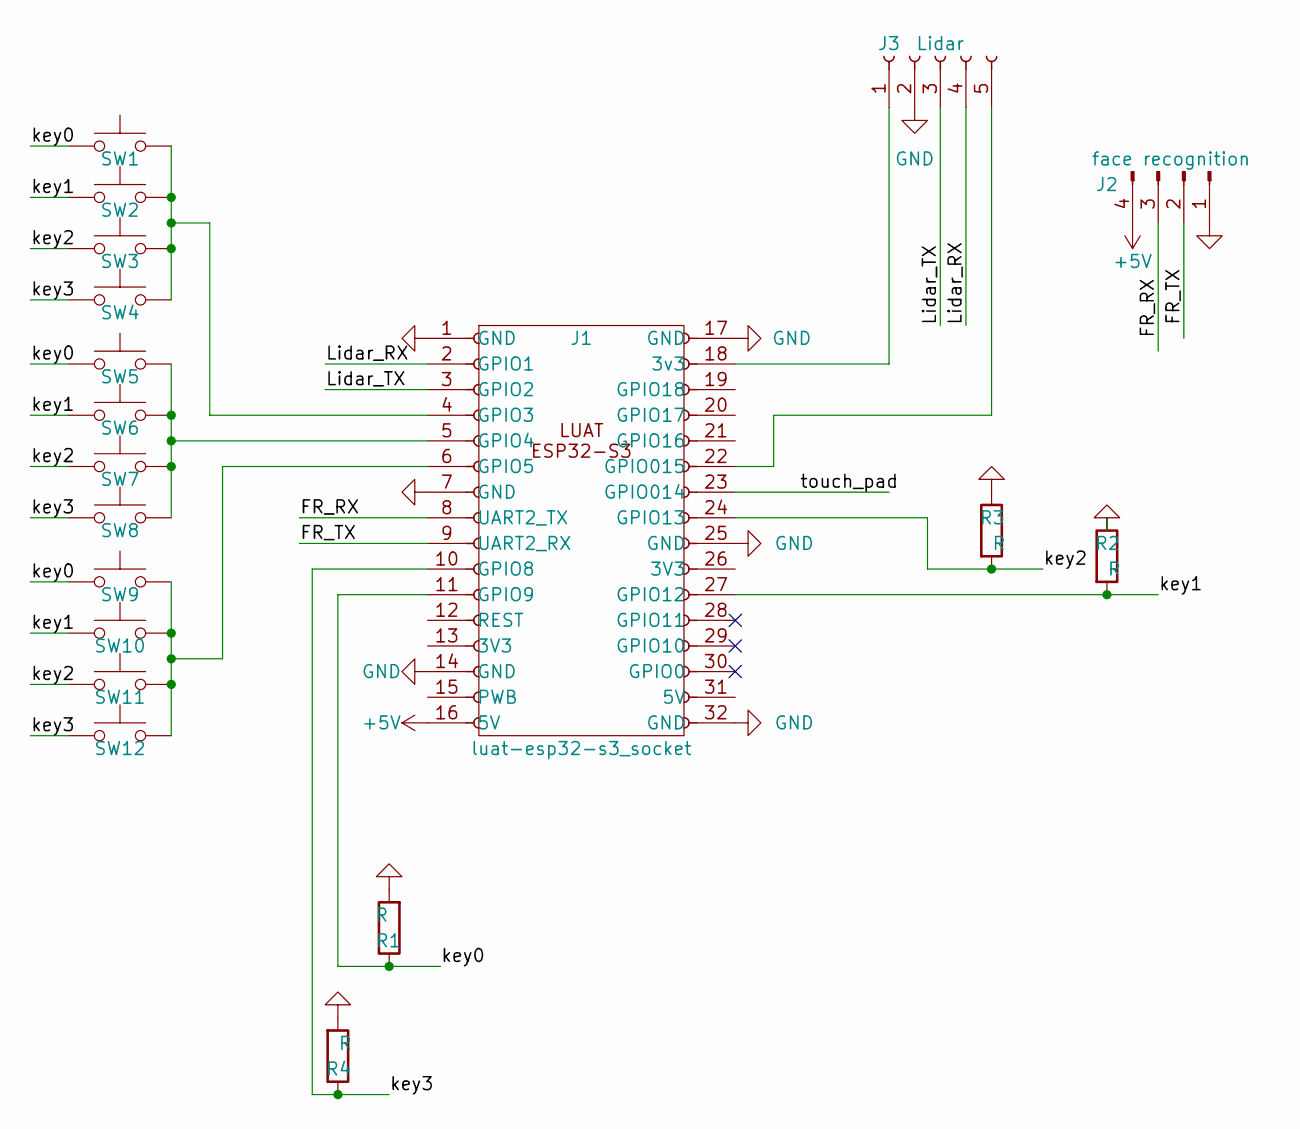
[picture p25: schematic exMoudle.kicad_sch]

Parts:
J1: luat-esp32-s3_socket; luat-esp32-s3-devBoard
J2: face recognition; PinHeader_1x04_P2.54mm_Vertical
J3: Lidar; PinSocket_1x05_P2.54mm_Vertical
R1, R2, R3, R4: R; R_Axial_DIN0207_L6.3mm_D2.5mm_P10.16mm_Horizontal
SW1, SW2, SW3, SW4, SW5, SW6, SW7, SW8, SW9, SW10, SW11, SW12: SW_Push; SW_Cherry_MX_1.00u_Plate

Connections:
+5V: J1.16 (5V), J2.4
/FR_RX: J1.8 (UART2_TX), J2.3
/FR_TX: J1.9 (UART2_RX), J2.2
/Lidar_RX: J1.2 (GPIO1), J3.4
/Lidar_TX: J1.3 (GPIO2), J3.3
/key0: J1.11 (GPIO9), R1.1, SW1.1, SW5.1, SW9.1
/key1: J1.27 (GPIO12), R2.2, SW2.1, SW6.1, SW10.1
/key2: J1.24 (GPIO13), R3.2, SW3.1, SW7.1, SW11.1
/key3: J1.10 (GPIO8), R4.1, SW4.1, SW8.1, SW12.1
/touch_pad: J1.23 (GPIO014)
GND: J1.1 (GND), J1.7 (GND), J1.14 (GND), J1.17 (GND), J1.25 (GND), J1.32 (GND), J2.1, J3.2, R1.2, R2.1, R3.1, R4.2
unnamed: J1.18 (3v3), J3.1
unnamed: J1.4 (GPIO3), SW1.2, SW2.2, SW3.2, SW4.2
unnamed: J1.5 (GPIO4), SW5.2, SW6.2, SW7.2, SW8.2
unnamed: J1.6 (GPIO5), SW9.2, SW10.2, SW11.2, SW12.2
unnamed: J1.22 (GPIO015), J3.5

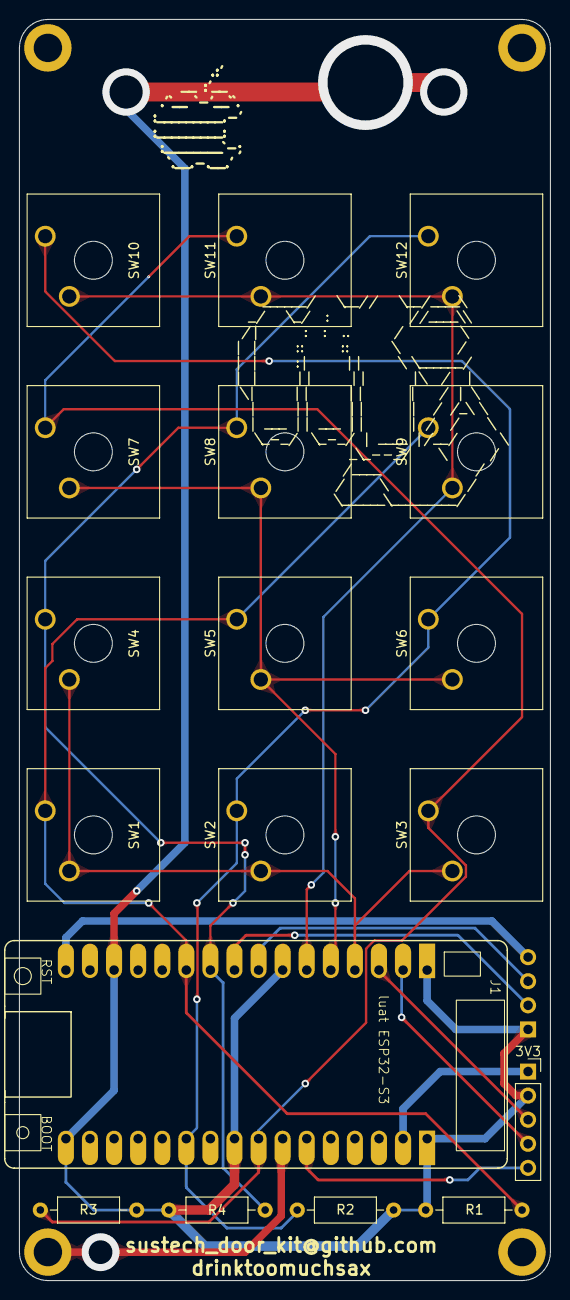
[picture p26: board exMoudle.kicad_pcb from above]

Board: 2 copper layers, 56.0 x 133.0 mm, 19 parts (1 on the bottom side), 15 nets.

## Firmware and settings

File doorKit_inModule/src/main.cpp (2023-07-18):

/**COPYRIGHT DELARE */
/*********
Rui Santos
Complete instructions at https://RandomNerdTutorials.com/esp32-ble-server-client/
Permission is hereby granted, free of charge, to any person obtaining a copy of this software and associated documentation files.
The above copyright notice and this permission notice shall be included in all copies or substantial portions of the Software.
*********/
/*
  Rui Santos
  Complete project details at https://RandomNerdTutorials.com/esp32-client-server-wi-fi/

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
  The above copyright notice and this permission notice shall be included in all
  copies or substantial portions of the Software.
*/
/**
 * @author drinktoomuchsax@github.com
 * @date 2023-07-18
 * @copyright The copyright notice and this permission notice shall be included in all copies or substantial portions of the Software.
 */
#include <Arduino.h>
#include <WiFi.h>

// WIFI part
const char *ssid = "1106-SBPool-Door_1";
const char *password = "01234567";
WiFiServer server(80);
String header;

// key and led part
const int lockRED = 6;
const int openDoor = 7;
String gpio23 = "off";
String gpio22 = "off";
String openDoorState = "off";
String lockREDState = "off";
const int lockRedInput = 12; // two input key(open and lock)
const int openDoorInput = 18;
const int ledGreen = 13;
// door operate

void setHigh(int whichPin)
{
  digitalWrite(lockRED, LOW);
  digitalWrite(openDoor, LOW);
  digitalWrite(whichPin, HIGH);
}
void operateDoor(String operate) // dircetly operate Door
{
  if (operate == "standby")
  {
    openDoorState = "off";
    lockREDState = "off";
    digitalWrite(openDoor, LOW);
    digitalWrite(lockRED, LOW);
  }
  else if (operate == "open")
  {
    openDoorState = "on";
    lockREDState = "off";
    digitalWrite(openDoor, HIGH);
    digitalWrite(lockRED, LOW);
  }
  else if (operate == "lock")
  {
    openDoorState = "off";
    lockREDState = "on";
    digitalWrite(openDoor, LOW);
    digitalWrite(lockRED, HIGH);
  }
}
void switchBetweenOpen(bool DELAY) // swith Openstate
{
  if (openDoorState == "on")
  {
    operateDoor("standby");
    Serial.println("open off");
    if (DELAY)
      delay(500);
  }
  else if (openDoorState == "off")
  {
    operateDoor("open");
    Serial.println("open on");
    if (DELAY)
      delay(500);
  }
}
void switchBetweenLock(bool DELAY)
{
  if (lockREDState == "on")
  {
    operateDoor("standby");
    Serial.println("lock off");
    if (DELAY)
      delay(500);
  }
  else if (lockREDState == "off")
  {
    operateDoor("lock");
    Serial.println("lock on");
    if (DELAY)
      delay(500);
  }
}

// BLE part
#include "BLEDevice.h"
#define bleServerName "1106_door_kit"                                          // BLE Server name (the other ESP32 name running the server sketch)
static BLEUUID doorServiceUUID("91bad492-b950-4226-aa2b-4ede9fa42f59");        /* UUID's of the service, characteristic that we want to read*/
static BLEUUID openCharacteristicUUID("cba1d466-344c-4be3-ab3f-189f80dd7518"); // open Characteristics
static BLEUUID lockCharacteristicUUID("ca73b3ba-39f6-4ab3-91ae-186dc9577d99"); // lock Characteristic
static boolean doConnect = false;                                              // Flags stating if should begin connecting and if the connection is up
static boolean connected = false;
static BLEAddress *pServerAddress;                  // Address of the peripheral device. Address will be found during scanning...
static BLERemoteCharacteristic *openCharacteristic; // Characteristicd that we want to read
static BLERemoteCharacteristic *lockCharacteristic;
const uint8_t notificationOn[] = {0x1, 0x0}; // Activate notify
const uint8_t notificationOff[] = {0x0, 0x0};
char *openChar; // Variables to store temperature and humidity
char *lockChar;
boolean newOpen = false; // Flags to check whether new temperature and humidity readings are available
boolean newLock = false;

static void openNotifyCallback(BLERemoteCharacteristic *pBLERemoteCharacteristic,
                               uint8_t *pData, size_t length, bool isNotify) // When the BLE Server sends a new open reading with the notify property

{
  openChar = (char *)pData;
  newOpen = true;
  Serial.println(*openChar);
  if (*openChar == 'o')
  {
    switchBetweenOpen(true);
    delay(10000);
    switchBetweenOpen(true);
  }
}

static void lockNotifyCallback(BLERemoteCharacteristic *pBLERemoteCharacteristic,
                               uint8_t *pData, size_t length, bool isNotify)

{
  lockChar = (char *)pData;
  newLock = true;
  Serial.println(*lockChar);
  if (*openChar == 'l')
  {
    switchBetweenLock(true);
  }
}

bool connectToServer(BLEAddress pAddress) // Connect to the BLE Server that has the name, Service, and Characteristics
{
  BLEClient *pClient = BLEDevice::createClient();
  pClient->connect(pAddress); // Connect to the remove BLE Server.
  Serial.println(" - Connected to server");
  BLERemoteService *pRemoteService = pClient->getService(doorServiceUUID); // Obtain a reference to the service we are after in the remote BLE server.
  if (pRemoteService == nullptr)
  {
    Serial.print("Failed to find our service UUID: ");
    Serial.println(doorServiceUUID.toString().c_str());
    return (false);
  }
  openCharacteristic = pRemoteService->getCharacteristic(openCharacteristicUUID); // Obtain a reference to the characteristics in the service of the remote BLE server.
  lockCharacteristic = pRemoteService->getCharacteristic(lockCharacteristicUUID);
  if (openCharacteristic == nullptr || lockCharacteristic == nullptr)
  {
    Serial.print("Failed to find our characteristic UUID");
    return false;
  }
  Serial.println(" - Found our characteristics");
  openCharacteristic->registerForNotify(openNotifyCallback); // Assign callback functions for the Characteristics
  lockCharacteristic->registerForNotify(lockNotifyCallback);
  return true;
}
class MyAdvertisedDeviceCallbacks : public BLEAdvertisedDeviceCallbacks // Callback function that gets called, when another device's advertisement has been received
{
  void onResult(BLEAdvertisedDevice advertisedDevice)
  {
    if (advertisedDevice.getName() == bleServerName) // Check if the name of the advertiser matches
    {
      advertisedDevice.getScan()->stop();                             // Scan can be stopped, we found what we are looking for
      pServerAddress = new BLEAddress(advertisedDevice.getAddress()); // Address of advertiser is the one we need
      doConnect = true;                                               // Set indicator, stating that we are ready to connect
      Serial.println("Device found. Connecting!");
    }
  }
};

void setup()
{
  Serial.begin(115200);

  // set gpio pin
  pinMode(lockRED, OUTPUT);
  pinMode(openDoor, OUTPUT);
  digitalWrite(lockRED, LOW);
  digitalWrite(openDoor, LOW);
  pinMode(lockRedInput, INPUT);
  pinMode(openDoorInput, INPUT);
  pinMode(ledGreen, OUTPUT);
  digitalWrite(ledGreen, LOW);

  // WIFI part
  Serial.println("Setting AP (Access Point)…");
  WiFi.mode(WIFI_AP);
  WiFi.softAP(ssid, password); // launch the access point
  Serial.println("Wait 100 ms for AP_START...");
  delay(100);
  Serial.println("Setting the AP");
  IPAddress Ip(192, 168, 110, 6); // setto IP Access Point same as gateway
  IPAddress NMask(255, 255, 255, 0);
  WiFi.softAPConfig(Ip, Ip, NMask);
  IPAddress ip = WiFi.softAPIP();
  Serial.print("AP IP address: ");
  Serial.println(ip);
  server.begin();

  // BLE part
  Serial.println("Starting Arduino BLE Client application...");
  BLEDevice::init(""); // Init BLE device
  // Retrieve a Scanner and set the callback we want to use to be informed when we have detected a new device.  Specify that we want active scanning and start the scan to run for 30 seconds.
  BLEScan *pBLEScan = BLEDevice::getScan();
  pBLEScan->setAdvertisedDeviceCallbacks(new MyAdvertisedDeviceCallbacks());
  pBLEScan->setActiveScan(true);
  pBLEScan->start(30);
}

void loop()
{
  // BLE part
  if (doConnect == true)
  {
    if (connectToServer(*pServerAddress))
    {
      Serial.println("We are now connected to the BLE Server."); // Activate the Notify property of each Characteristic
      openCharacteristic->getDescriptor(BLEUUID((uint16_t)0x2902))->writeValue((uint8_t *)notificationOn, 2, true);
      lockCharacteristic->getDescriptor(BLEUUID((uint16_t)0x2902))->writeValue((uint8_t *)notificationOn, 2, true);
      connected = true;
    }
    else
    {
      Serial.println("We have failed to connect to the server; Restart your device to scan for nearby BLE server again.");
      digitalWrite(ledGreen, HIGH);
    }
    doConnect = false;
  }

  if (newOpen && newLock)
  {
    newOpen = false;
    newLock = false;
  }

  // press upper key set door open(clear other state), press lower key set door lock(clear other state), press both clear all
  if ((digitalRead(openDoorInput) == 1) && (digitalRead(lockRedInput) != 1))
  {
    switchBetweenOpen(true);
  }
  else if ((digitalRead(openDoorInput) != 1) && (digitalRead(lockRedInput) == 1))
  {
    switchBetweenLock(true);
  }
  else if ((digitalRead(openDoorInput) == 1) && (digitalRead(lockRedInput) == 1))
  {
    operateDoor("standby");
    delay(2000);
  }

  // blinking led
  if (openDoorState == "on")
  {
    digitalWrite(ledGreen, HIGH);
  }
  else if (openDoorState == "off")
  {
    digitalWrite(ledGreen, LOW);
  }

  if (lockREDState == "on")
  {
    digitalWrite(ledGreen, HIGH);
    delay(80);
    digitalWrite(ledGreen, LOW);
    delay(80);
  }
  else
  {
    digitalWrite(ledGreen, LOW);
  }

  // WIFI part copy from https://randomnerdtutorials.com/esp32-web-server-arduino-ide/,if you want to know how these code works, learn details there.
  WiFiClient client = server.available(); // Listen for incoming clients
  if (client)
  {                                // If a new client connects,
    Serial.println("New Client."); // print a message out in the serial port
    String currentLine = "";       // make a String to hold incoming data from the client
    int timeout = 0;
    while (client.connected())
    { // loop while the client's connected
      timeout++;
      if (client.available())
      {                         // if there's bytes to read from the client,
        char c = client.read(); // read a byte, then
        Serial.write(c);        // print it out the serial monitor
        header += c;
        if (c == '\n')
        {
          if (currentLine.length() == 0)
          {
            // HTTP headers always start with a response code (e.g. HTTP/1.1 200 OK)
            // and a content-type so the client knows what's coming, then a blank line:
            client.println("HTTP/1.1 200 OK");
            client.println("Content-type:text/html");
            client.println("Connection: close");
            client.println();

            // turns the GPIOs on and off
            if (header.indexOf("GET /openDoorState/on") >= 0)
            {
              Serial.println("/openDoorState/on");
              operateDoor("open");
            }
            else if (header.indexOf("GET /openDoorState/off") >= 0)
            {
              Serial.println("/openDoorState/off");
              operateDoor("standby");
            }
            else if (header.indexOf("GET /lockREDState/on") >= 0)
            {
              Serial.println("/lockREDState/on");
              operateDoor("lock");
            }
            else if (header.indexOf("GET /lockREDState/off") >= 0)
            {
              Serial.println("/lockREDState/off");
              operateDoor("standby");
            }

            // Display the HTML web page
            client.println("<!DOCTYPE html><html>");
            client.println("<head><meta name=\"viewport\" content=\"width=device-width, initial-scale=1\">");
            client.println("<link rel=\"icon\" href=\"data:,\">");
            // CSS to style the on/off buttons
            // Feel free to change the background-color and font-size attributes to fit your preferences
            client.println("<style>html { font-family: Helvetica; display: inline-block; margin: 0px auto; text-align: center;}");
            client.println(".button { display: inline-block; padding: 15px 25px; font-size: 24px; cursor: pointer; text-align: center; text-decoration: none; outline: none;");
            client.println("color: #fff; background-color: #4CAF50; border: none; border-radius: 15px; box-shadow: 0 9px #999;}");
            client.println("button:hover { background-color: #3e8e41 }");
            client.println("button:active { background-color: #3e8e41; box-shadow: 0 5px #666; transform: translateY(4px); }");
            client.println(".button2 {background-color: #555555;}</style></head>");

            // Web Page Heading
            client.println("<body><h1>ESP32 Web Server</h1>");

            // Display current state, and ON/OFF buttons for GPIO 26
            client.println("<p>OpenSwitch " + openDoorState + "</p>");
            // If the openDoorState is off, it displays the ON button
            if (openDoorState == "off")
            {
              client.println("<p><a href=\"/openDoorState/on\"><button class=\"button\">ON</button></a></p>");
            }
            else
            {
              client.println("<p><a href=\"/openDoorState/off\"><button class=\"button button2\">OFF</button></a></p>");
            }

            // Display current state, and ON/OFF buttons for GPIO 27
            client.println("<p>LockSwitch " + lockREDState + "</p>");
            // If the lockREDState is off, it displays the ON button
            if (lockREDState == "off")
            {
              client.println("<p><a href=\"/lockREDState/on\"><button class=\"button\">ON</button></a></p>");
            }
            else
            {
              client.println("<p><a href=\"/lockREDState/off\"><button class=\"button button2\">OFF</button></a></p>");
            }
            client.println("</body></html>");

            // The HTTP response ends with another blank line
            client.println();
            // Break out of the while loop
            break;
          }
          else
          { // if you got a newline, then clear currentLine
            currentLine = "";
          }
        }
        else if (c != '\r')
        {                   // if you got anything else but a carriage return character,
          currentLine += c; // add it to the end of the currentLine
        }
      }
      else if (timeout > 1000 ^ 1000 ^ 1000) // 40Mhz
      {
        break;
      }
    }
    // Clear the header variable
    header = "";
    // Close the connection
    client.stop();
    Serial.println("Client disconnected.");
    Serial.println("");
  }
}

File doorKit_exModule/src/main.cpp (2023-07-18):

/**COPYRIGHT DELARE */
/*********
Rui Santos
Complete instructions at https://RandomNerdTutorials.com/esp32-ble-server-client/
Permission is hereby granted, free of charge, to any person obtaining a copy of this software and associated documentation files.
The above copyright notice and this permission notice shall be included in all copies or substantial portions of the Software.
*********/
/*
  Rui Santos
  Complete project details at https://RandomNerdTutorials.com/esp32-client-server-wi-fi/

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
  The above copyright notice and this permission notice shall be included in all
  copies or substantial portions of the Software.
*/
/**
 * @author drinktoomuchsax@github.com
 * @date 2023-07-18
 * @copyright The copyright notice and this permission notice shall be included in all copies or substantial portions of the Software.
 */

#include <Arduino.h>
// keyboard part
#include <vector>
using namespace std;
// STATE indicate the state of esp32. It could be syandby, verifyPSWD_wipeJitter, undifened and etc
String STATE = "undifeined";

// BLE part
#include <BLEDevice.h>
#include <BLEServer.h>
#include <BLEUtils.h>
#include <BLE2902.h>
#define bleServerName "1106_door_kit" // BLE server name
bool deviceConnected = false;
#define SERVICE_UUID "91bad492-b950-4226-aa2b-4ede9fa42f59"                                                        // See the following for generating UUIDs: https://www.uuidgenerator.net/
BLECharacteristic openCharacteristics("cba1d466-344c-4be3-ab3f-189f80dd7518", BLECharacteristic::PROPERTY_NOTIFY); // open Characteristic and Descriptor
BLEDescriptor openDescriptor(BLEUUID((uint16_t)0x2902));
BLECharacteristic lockCharacteristics("ca73b3ba-39f6-4ab3-91ae-186dc9577d99", BLECharacteristic::PROPERTY_NOTIFY); // lock Characteristic and Descriptor
BLEDescriptor lockDescriptor(BLEUUID((uint16_t)0x2903));
class MyServerCallbacks : public BLEServerCallbacks // Setup callbacks onConnect and onDisconnect
{
  void onConnect(BLEServer *pServer)
  {
    deviceConnected = true;
  };
  void onDisconnect(BLEServer *pServer)
  {
    deviceConnected = false;
  }
};
/*
 | "o"   | open the door |
 | "l"   | lock the door |
 | "u"   | unlock       |*/
char oPen = 'o';
char lock = 'l';
char unlock = 'u';
bool OPEN = true;
bool LOCK = false;
void sendSignal(char signal, bool openORlock)
{
  if (openORlock)
  {
    char SIGNAL[] = {signal};
    openCharacteristics.setValue(SIGNAL);
    openCharacteristics.notify();
  }
  else if (!openORlock)
  {
    char SIGNAL[] = {signal};
    lockCharacteristics.setValue(SIGNAL);
    lockCharacteristics.notify();
  }
}

// keyboard part
#include <keyboardMatrix.h>
// keyboard part set your password in keyboardMatrix lib
vector<int> pswd;                  // initialize a password vector(array) to store the key user press
vector<int> realpswd;              // realpswd
int keyboardOutput[3] = {3, 4, 5}; // defining gpio output pin
#define key0 9
#define key1 12
#define key2 13
#define key3 8
int keyboardInput[4] = {key0, key1, key2, key3}; // defining gpio input pin
unsigned long lastTime = 0;                      // input timeout
unsigned long timerDelay = 30000;                // 30s

// face recognition part
// face recognition part
// #include <fr1002.h>
HardwareSerial SERfr1002(2); // rename Serial2 into SERfr1002 (stand for serial for fr1002)
uint8_t set_standby[6] = {0xEF, 0xAA, 0x23, 0x00, 0x00, 0x23};
uint8_t get_status[6] = {0xEF, 0xAA, 0x11, 0x00, 0x00, 0x11};
uint8_t go_recognization[8] = {0xEF, 0xAA, 0x12, 0x00, 0x02, 0x00, 0x0A, 0x1A}; // timeout 10s, parity is 0x1A
uint8_t get_usernameANDid[6] = {0xEF, 0xAA, 0x24, 0x00, 0x00, 0x24};

// led setup
const int ledA = 10;
const int ledB = 11;
bool testState = false;
bool lockState = false;

void ledBlink(int whichLed, int circleTime, int gapTime)
{
  if (circleTime > 0)
  {
    for (int Z = 0; Z < circleTime; Z++)
    {
      digitalWrite(whichLed, HIGH);
      delay(gapTime);
      digitalWrite(whichLed, LOW);
      delay(gapTime);
    }
  }
  if (lockState) // long light for lockLED red
    digitalWrite(ledB, HIGH);
  else
    digitalWrite(ledB, LOW);
}

bool switchState(bool state) // switch testState or lockState
{
  if (testState)
  {
    Serial.println("switchState is here");
  }
  if (state)
  {
    if (testState)
      Serial.println("ops false");
    return false;
  }
  else
  {
    if (testState)
      Serial.println("ops true");
    return true;
  }
}

void setup()
{
  Serial.begin(115200);

  // SERfr1002.begin(115200, SERIAL_8N1, 16, 17); // uart port for hlk-fr1002 face recogniton module with baud rate 115200 bps, 8_data_bit, No_parity, 1_stop_bit

  // led setup
  pinMode(ledA, OUTPUT);
  pinMode(ledB, OUTPUT);

  // BLE setup
  BLEDevice::init(bleServerName);                 // Create the BLE Device
  BLEServer *pServer = BLEDevice::createServer(); // Create the BLE Server
  pServer->setCallbacks(new MyServerCallbacks());
  BLEService *doorService = pServer->createService(SERVICE_UUID); // Create the BLE Service
  doorService->addCharacteristic(&openCharacteristics);           // Create BLE Characteristics and Create a BLE Descriptor
  openDescriptor.setValue("open door signal");
  openCharacteristics.addDescriptor(&openDescriptor);
  doorService->addCharacteristic(&lockCharacteristics);
  lockDescriptor.setValue("lock door signal");
  lockCharacteristics.addDescriptor(new BLE2902());
  doorService->start();                                       // Start the service
  BLEAdvertising *pAdvertising = BLEDevice::getAdvertising(); // Start advertising
  pAdvertising->addServiceUUID(SERVICE_UUID);
  pServer->getAdvertising()->start();
  Serial.println("Waiting a client connection to notify...");
}
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

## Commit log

2023-06-26 add local file
    [result.xlsx]
2023-06-26 增加挟持保护功能
2023-06-27 add fr1002 stm32 example
2023-07-03 add pcb design
    [exModule.kicad_pcb, exModule.kicad_sch]
2023-07-03 switch to cable
2023-07-03 change to cable
2023-07-03 阿萨大大、
2023-07-03 update inModule button
2023-07-04 change to cheaper esp32-c3
2023-07-05 更新exMoudle pcb，readme增加BOM
    [exModule-B_Cu.gbl, exModule-B_Mask.gbs, exModule-B_Paste.gbp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]
2023-07-05 change logo to cable
2023-07-06 update exModule pcb layout
    [exMoudle-B_Cu.gbl, exMoudle-B_Mask.gbs, exMoudle-B_Paste.gbp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]
2023-07-06 updare exModule pcb
    [exMoudle.kicad_pcb]
2023-07-08 change exModule to esp32-s3
2023-07-09 uodate exModule pcb keyboard
    [exMoudle.kicad_pcb, exMoudle.kicad_sch]
2023-07-09 update inModule pcb add relay holes
    [inModule.kicad_pcb, inModule.kicad_sch]
2023-07-09 uodate inModule change gpio define
    [inModule.kicad_pcb, inModule.kicad_sch]
2023-07-10 add blinking led in exModule
2023-07-10 back up
    [exModule-B_Cu.gbl, exModule-B_Mask.gbs, exModule-B_Paste.gbp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]
2023-07-11 i delete the repo then i clone it from github
    [exModule-B_Cu.gbl, exModule-B_Mask.gbs, exModule-B_Paste.gbp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]
2023-07-14 figure out cable communication is impossiable
2023-07-17 fix inMoudle html open lock state both survive bug
    [main.cpp]
2023-07-17 fix inModule html both open and lock state survive
    [main.cpp]
2023-07-17 update readme bom
2023-07-17 reamde add 南科手册
2023-07-18 bug fix for timeout in exModule
    [exModule_backup.cpp, exModule_backup_0.1.cpp, main.cpp]
